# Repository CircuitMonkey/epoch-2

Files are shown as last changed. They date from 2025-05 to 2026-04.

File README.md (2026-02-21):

# epoch-2
Epoch Vibrator Controller *(Haptic Field Emitter)* 2 - Now with 100% more edge...

## Description
A follow on to [Epoch 1](https://github.com/CircuitMonkey/epoch).  Designed in 2025. Replaced by [Epoch 3](https://github.com/CircuitMonkey/epoch-3) in 2026. Redesigned with [AdaFruit Qualia ESP32](https://www.adafruit.com/product/5800) and a [Amazon 4-inch IPS (GT911 touch)](https://www.amazon.com/dp/B0D9H3HWR3).  Motors driven with [pca9685 PWM controller](https://learn.adafruit.com/adafruit-16-channel-pwm-servo-hat-for-raspberry-pi)/[Amazon PCA9685 Board](https://www.amazon.com/dp/B0D73811V8) and FET outputs in order to drive bigger motors.  Epoch 1 was limited to 120mA maximum motor drive (because of PWM controller choice) and some larger "rumble" motors need 180mA or higher.

## Features
 - [Adafruit Qualia ESP32-S3 RGB666](https://www.adafruit.com/product/5800)
 - [Amazon 4-inch IPS (GT911 touch)](https://www.amazon.com/dp/B0D9H3HWR3)
 - [pca9685 PWM controller](https://learn.adafruit.com/adafruit-16-channel-pwm-servo-hat-for-raspberry-pi)
 - [LiPo Battery - 62mm x 50mm, 2500mAH, Adafruit](https://www.adafruit.com/product/328)
 - TRS 3.5mm type cables (two motors per connector)
 - FET outputs in order to drive bigger motors.
 - Used [Electric Mini Micro Vibration Motor DC 1.5V/3V/6V 1000RPM M20 with Brass Eccentric Rotating Wheel ](https://www.amazon.com/dp/B07X7MKKQH) in attachments.
 - Programmed in CircuitPython.

## Dev Notes
 - Hardware was intended to output all 16 channels as two rows of connectors, but only built one row.
 - IPS type display used most of the ESP32 pins.
 - Circuit Python with the IPS display was excrucatingly slow.
 - Touch response time was very slow with Circuit Python and made on-screen sliders frustrating to use.
 - TRS Audio type connectors were a big improvement over Molex MinifitJr type connectors.
 - This platform performed well for almost a year, before Epoch-3 developed.
 - Experimental air pressure input showed promise but was fussy in setup/use and not worth using long term.
 - PCA9685 PWM driver was much easier to code with over older Epoch-1 PWM driver.
 - FET outputs allowed use of slightly bigger motors with more rumble yet allowed for a lower motor speeds for subtle haptic sensations.
 - Custom molds were 3D printed for attachments where silicone was poured over a TPU flex frame that held the motors.
 - Attachments had LEDs built in to indicate intensity of each motor.
 - This design and motor patterns have changed my life, able to realize two or three hour long usage sessions.
 - I look forward to improving on this design in Epoch 3.

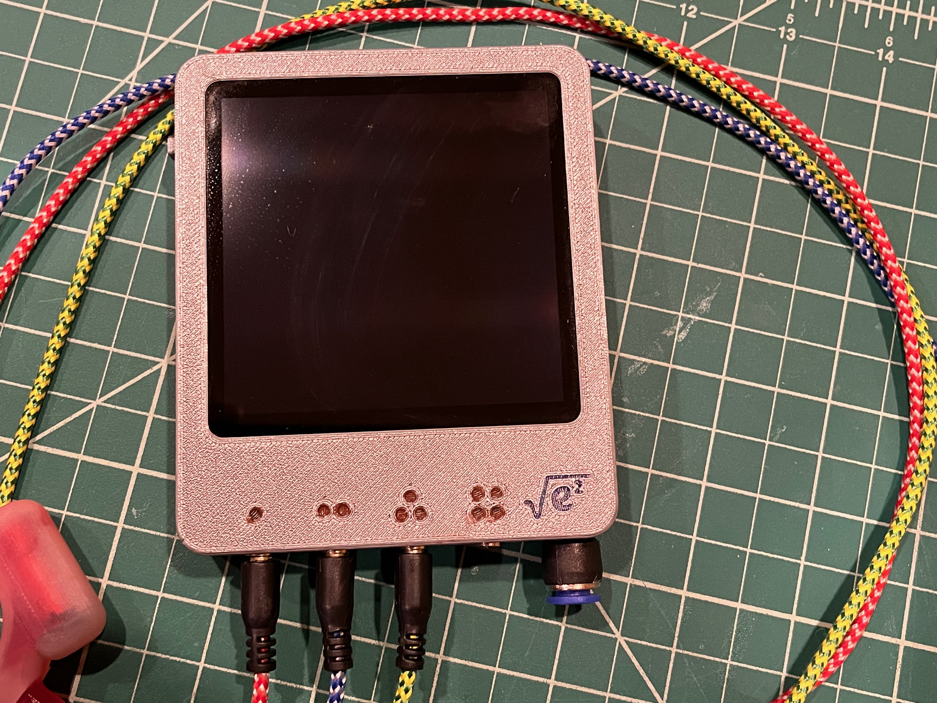
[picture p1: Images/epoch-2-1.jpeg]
Epoch 2 - Front View

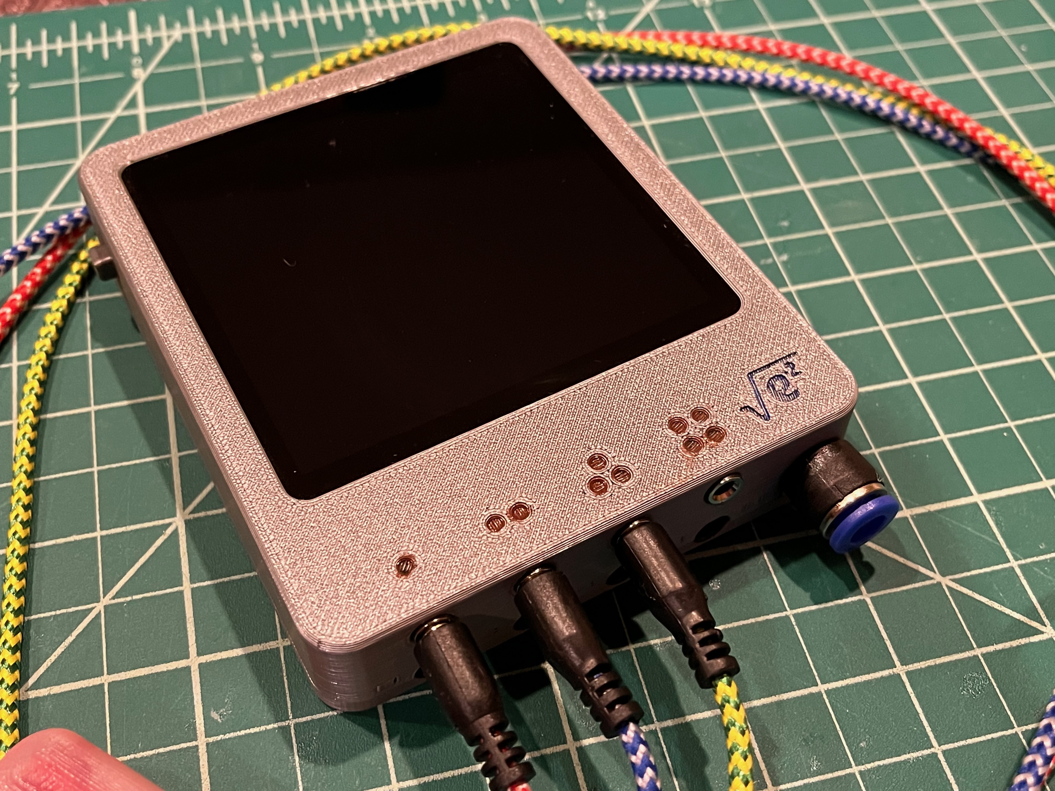
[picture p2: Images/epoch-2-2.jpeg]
Epoch 2 - Ortho View

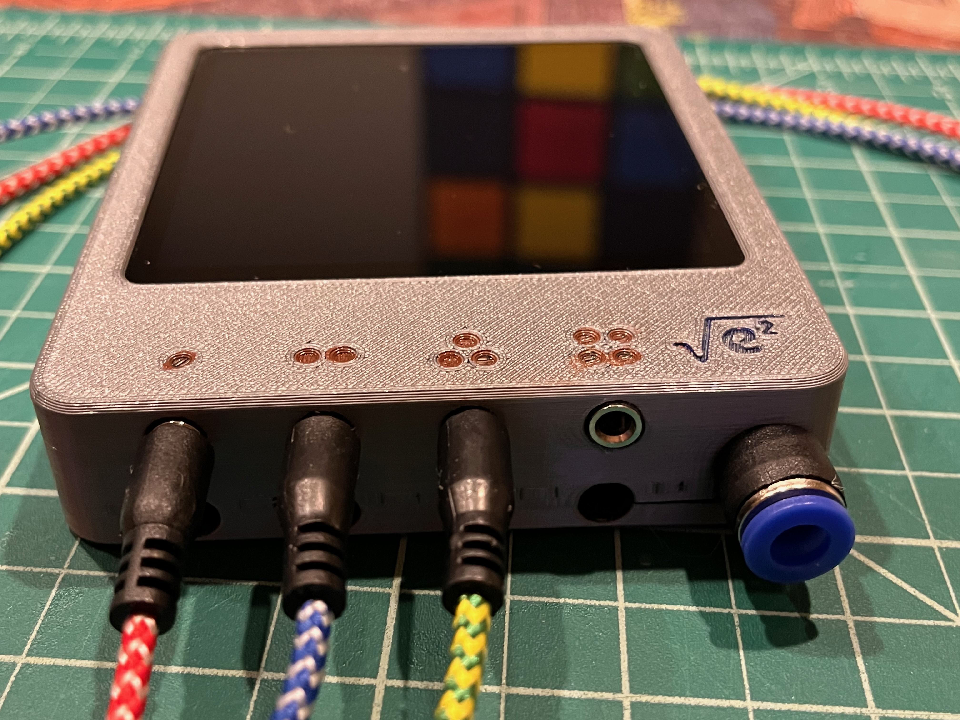
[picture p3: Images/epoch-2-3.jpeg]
Epoch 2 - Connector View

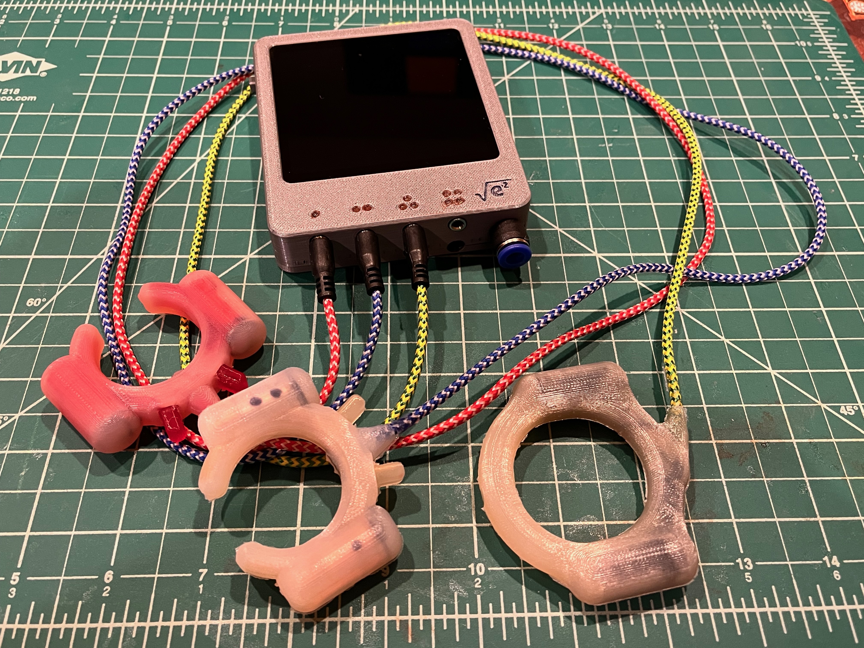
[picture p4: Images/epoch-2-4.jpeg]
Epoch 2 - With Attachments

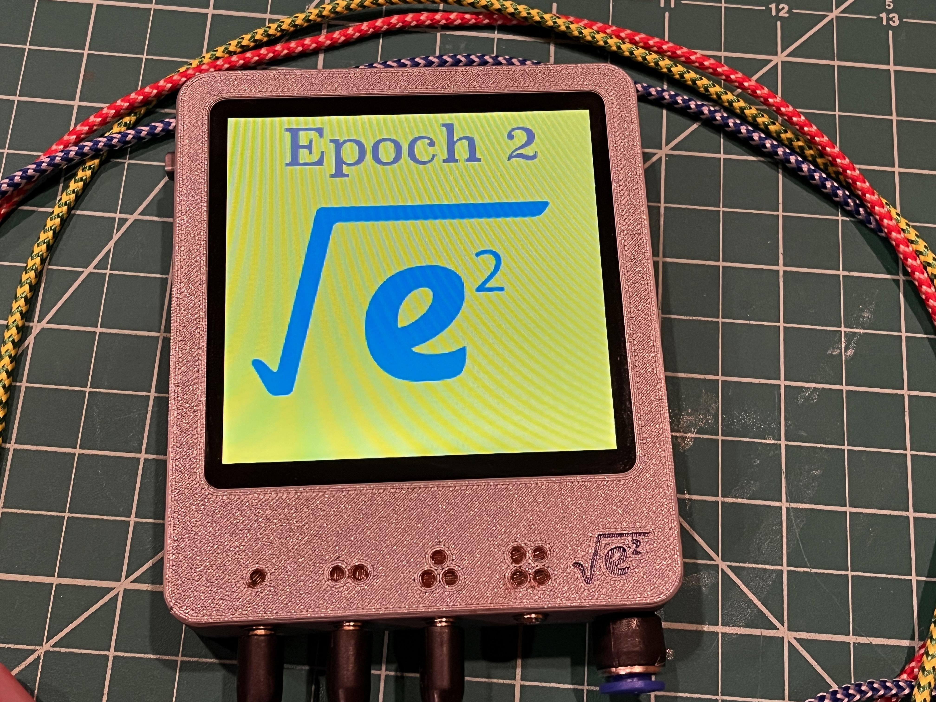
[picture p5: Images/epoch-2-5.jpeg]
Epoch 2 - Power On Screen

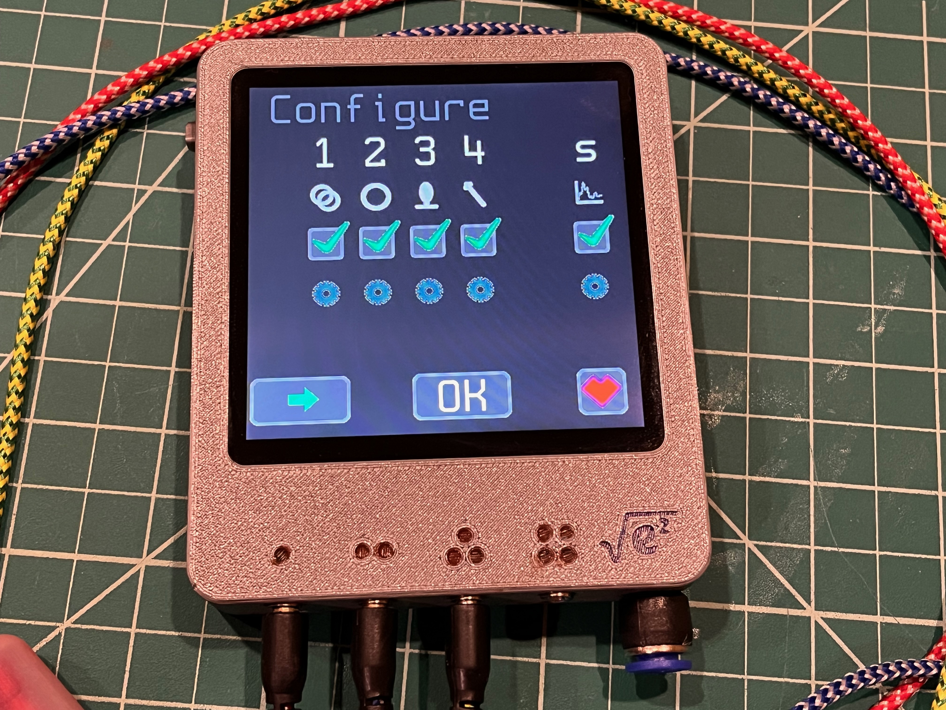
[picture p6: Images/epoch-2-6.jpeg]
Epoch 2 - Configuration Screen

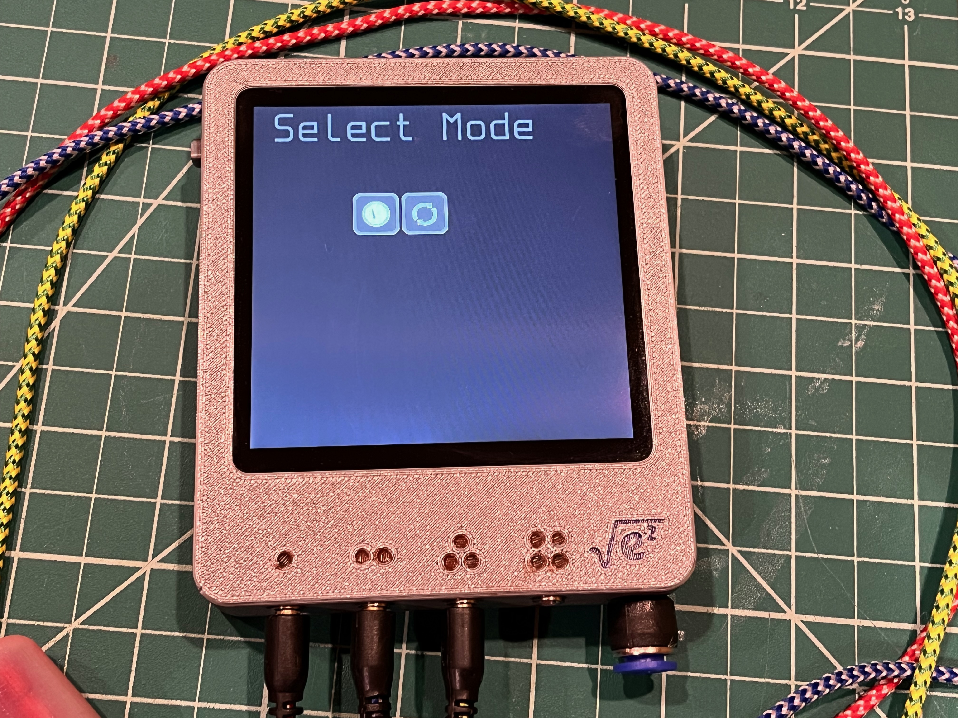
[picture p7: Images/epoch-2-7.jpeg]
Epoch 2 - Mode Select Screen

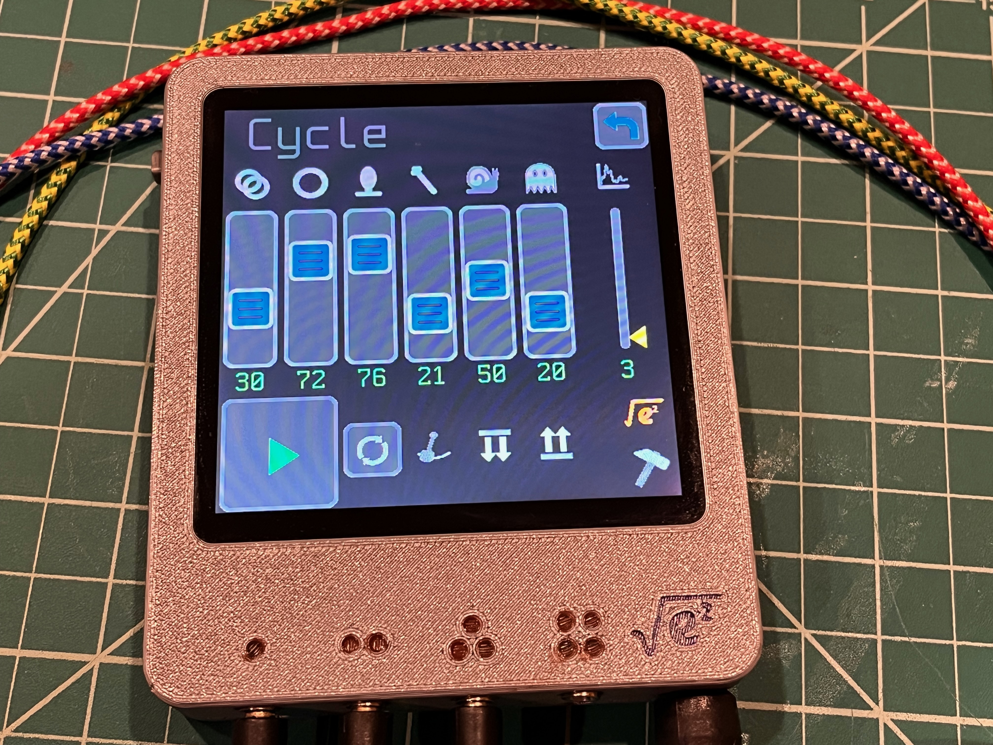
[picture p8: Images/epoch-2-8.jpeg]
Epoch 2 - Cycle Mode Screen

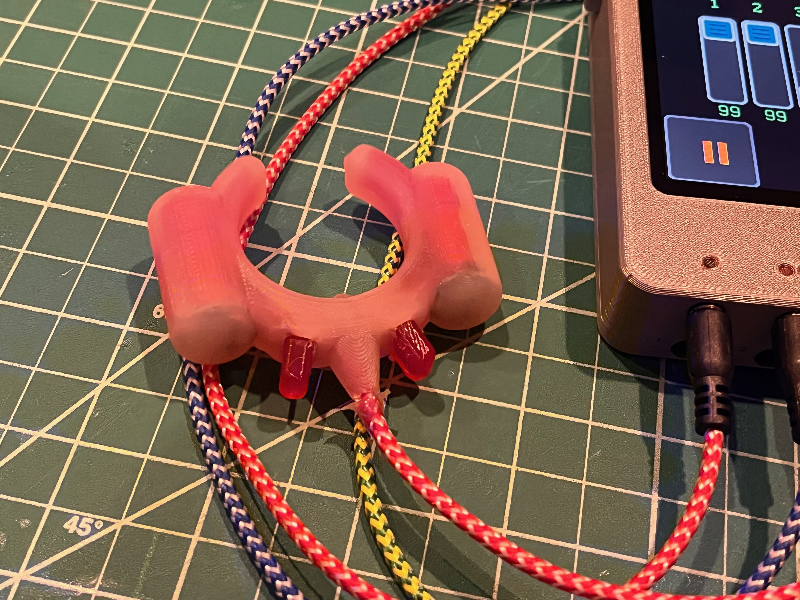
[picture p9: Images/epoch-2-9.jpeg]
Epoch 2 - Attachment Not-vibrating

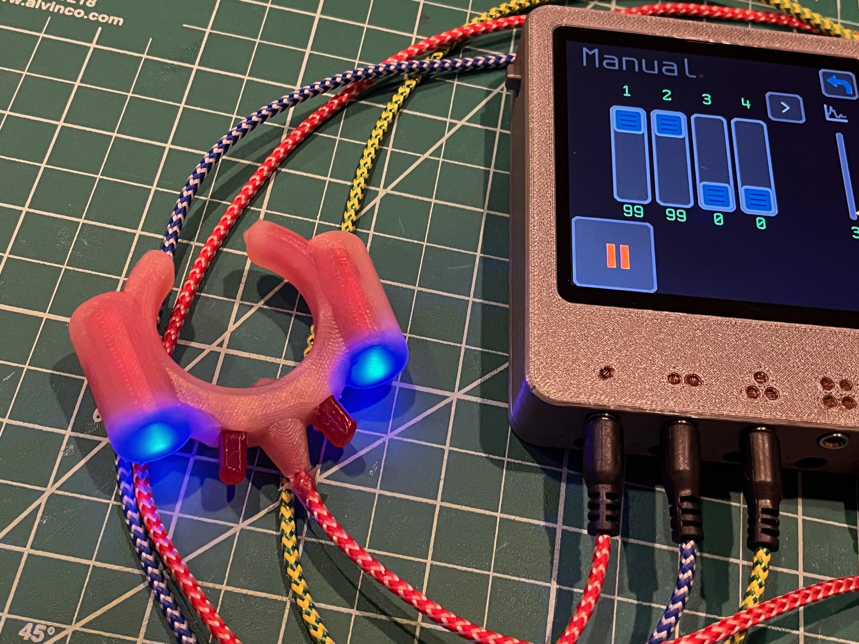
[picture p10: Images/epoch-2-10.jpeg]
Epoch 2 - Attachment Vibrating


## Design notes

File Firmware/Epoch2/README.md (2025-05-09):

# Main Program for Epoch 2

Place all files/dirs into Qualia CircuitPython drive root then reboot.

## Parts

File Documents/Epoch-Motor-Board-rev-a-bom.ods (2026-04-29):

Epoch Motor Board (Rev. A)
Reference | Qty | Value | Footprint
C1,C2,C3,C4 | 4 | 0.01uF/50V | Capacitor_SMD:C_0603_1608Metric
D1,D2,D3,D4 | 4 | BLU | LED_SMD:LED_0603_1608Metric
R1,R2,R3,R4 | 4 | 47R | Resistor_SMD:R_0603_1608Metric

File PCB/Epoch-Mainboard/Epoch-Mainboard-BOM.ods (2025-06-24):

Epoch 2 – Mainboard BOM |  | Rev. A – 2025/06
Reference | Qty | Value | Footprint | Datasheet
BAT1 | 1 | JST-PH | Connector_JST:JST_PH_S2B-PH-K_1x02_P2.00mm_Horizontal | ~
C1,C2 | 2 | 4.7uF/16V | Capacitor_SMD:C_0603_1608Metric | ~
C3 | 1 | 0.01uF | Capacitor_SMD:C_0603_1608Metric | ~
D1 | 1 | YEL | LED_SMD:LED_0603_1608Metric | ~
D2 | 1 | BLU | LED_SMD:LED_0603_1608Metric | ~
J1 | 1 | USB_C_Receptacle_PowerOnly_6P | Connector_USB:USB_C_Receptacle_HRO_TYPE-C-31-M-17 | https://www.usb.org/sites/default/files/documents/usb_type-c.zip
J2,J3 | 2 | Conn_02x06_Odd_Even | Connector_PinHeader_2.54mm:PinHeader_2x06_P2.54mm_Vertical | ~
R1,R2,R3,R4,R5,R6,R7 | 7 | 1K | Resistor_SMD:R_0603_1608Metric | ~
R8,R9 | 2 | 22K (pull up!) | Resistor_SMD:R_0603_1608Metric | ~
R10 | 1 | 2K | Resistor_SMD:R_0603_1608Metric | ~
R11,R12 | 2 | 2K | Resistor_SMD:R_0603_1608Metric | ~
R13,R14 | 2 | 0R | Resistor_SMD:R_1206_3216Metric | ~
R21,R22,R23,R24,R25,R26,R27,R28,R29,R30,R31,R32,R33,R34,R35,R36 | 16 | 220R | Resistor_SMD:R_0603_1608Metric | ~
SW1 | 1 | SW_SPDT | Button_Switch_THT:SW_Slide_SPDT_Angled_CK_OS102011MA1Q | ~
U1 | 1 | PCA9685PW | Package_SO:TSSOP-28_4.4x9.7mm_P0.65mm | http://www.nxp.com/docs/en/data-sheet/PCA9685.pdf
U2 | 1 | MCP73831T-2ACI/OT | Package_TO_SOT_SMD:SOT-23-5 | http://ww1.microchip.com/downloads/en/DeviceDoc/20001984g.pdf

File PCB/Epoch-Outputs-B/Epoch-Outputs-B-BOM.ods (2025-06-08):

Epoch 2 – Outputs B - BOM |  | Rev. A – 2025/06
Reference | Qty | Value | Footprint | Datasheet
C1,C2,C3,C4 | 4 | 22uF/16V | Capacitor_SMD:C_1812_4532Metric | ~
D1,D2,D3,D4,D5,D6,D7,D8 | 8 | NRVA4007T3G | Diode_SMD:D_SMA | http://www.onsemi.com/pub_link/Collateral/MRA4003T3-D.PDF
F1,F2,F3,F4 | 4 | MF-MSMF075 | Resistor_SMD:R_1812_4532Metric | ~
J1,J2,J3,J4 | 4 | Jack - Tayda A-4780 | Connector_Audio:Jack_3.5mm_CUI_SJ1-3515N_Horizontal | ~
J5 | 1 | Conn_02x06_Odd_Even | Connector_PinHeader_2.54mm:PinHeader_2x06_P2.54mm_Vertical | ~
Q1,Q2,Q3,Q4,Q5,Q6,Q7,Q8 | 8 | Si1308EDL | Package_TO_SOT_SMD:SOT-323_SC-70 | https://www.vishay.com/docs/63399/si1308edl.pdf
R1,R2,R3,R4,R5,R6,R7,R8 | 8 | 100R | Resistor_SMD:R_0603_1608Metric | ~
R9,R10,R11,R12,R13,R14,R15,R16 | 8 | 100K | Resistor_SMD:R_0603_1608Metric | ~

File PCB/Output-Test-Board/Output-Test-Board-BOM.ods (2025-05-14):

Epoch2 – Motor Test Board – Rev. A |  |  | 2025-05
Reference | Qty | Value | Footprint | Datasheet
C1 | 1 | 22uF / 16V | Capacitor_SMD:C_1812_4532Metric | ~
D1,D2 | 2 | GRN | LED_SMD:LED_0603_1608Metric | ~
D3,D4 | 2 | NRVA4007T3G | Diode_SMD:D_SMA | http://www.onsemi.com/pub_link/Collateral/MRA4003T3-D.PDF
F1 | 1 | MF-MSMF075 | Resistor_SMD:R_1812_4532Metric | ~
J1 | 1 | Conn_01x04_Pin | Connector_PinHeader_2.54mm:PinHeader_1x04_P2.54mm_Vertical | ~
J2 | 1 | Jack - Tayda A-4780 | Connector_Audio:Jack_3.5mm_Ledino_KB3SPRS_Horizontal | ~
Q1,Q2 | 2 | Si1308EDL | Package_TO_SOT_SMD:SOT-323_SC-70 | https://www.vishay.com/docs/63399/si1308edl.pdf
R1,R2,R3,R4 | 4 | 220R | Resistor_SMD:R_0603_1608Metric | ~
R5,R6 | 2 | 100K | Resistor_SMD:R_0603_1608Metric | ~

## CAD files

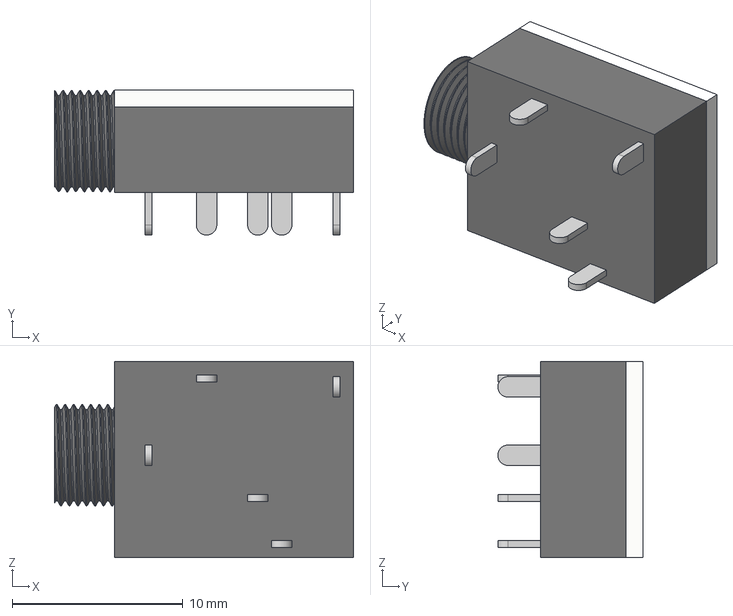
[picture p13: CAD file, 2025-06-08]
PCB/Epoch-Outputs-A/3D_models/A-069 v4.step
17.5 x 8.50 x 11.5 mm

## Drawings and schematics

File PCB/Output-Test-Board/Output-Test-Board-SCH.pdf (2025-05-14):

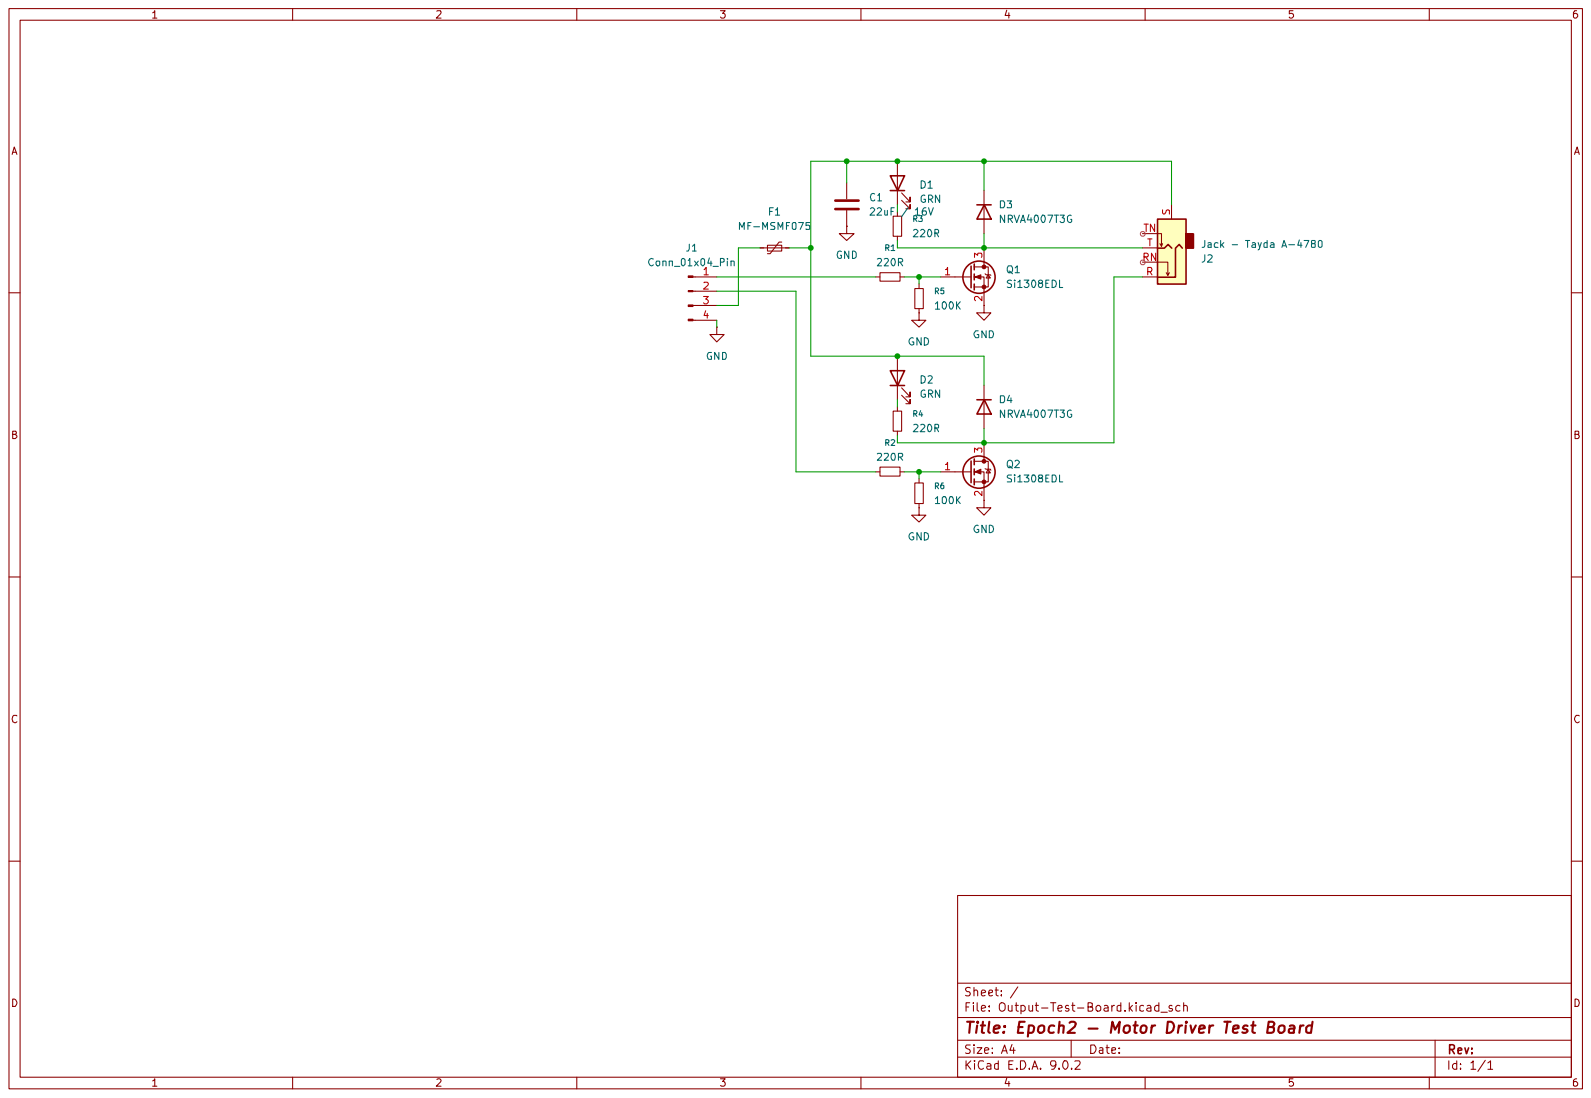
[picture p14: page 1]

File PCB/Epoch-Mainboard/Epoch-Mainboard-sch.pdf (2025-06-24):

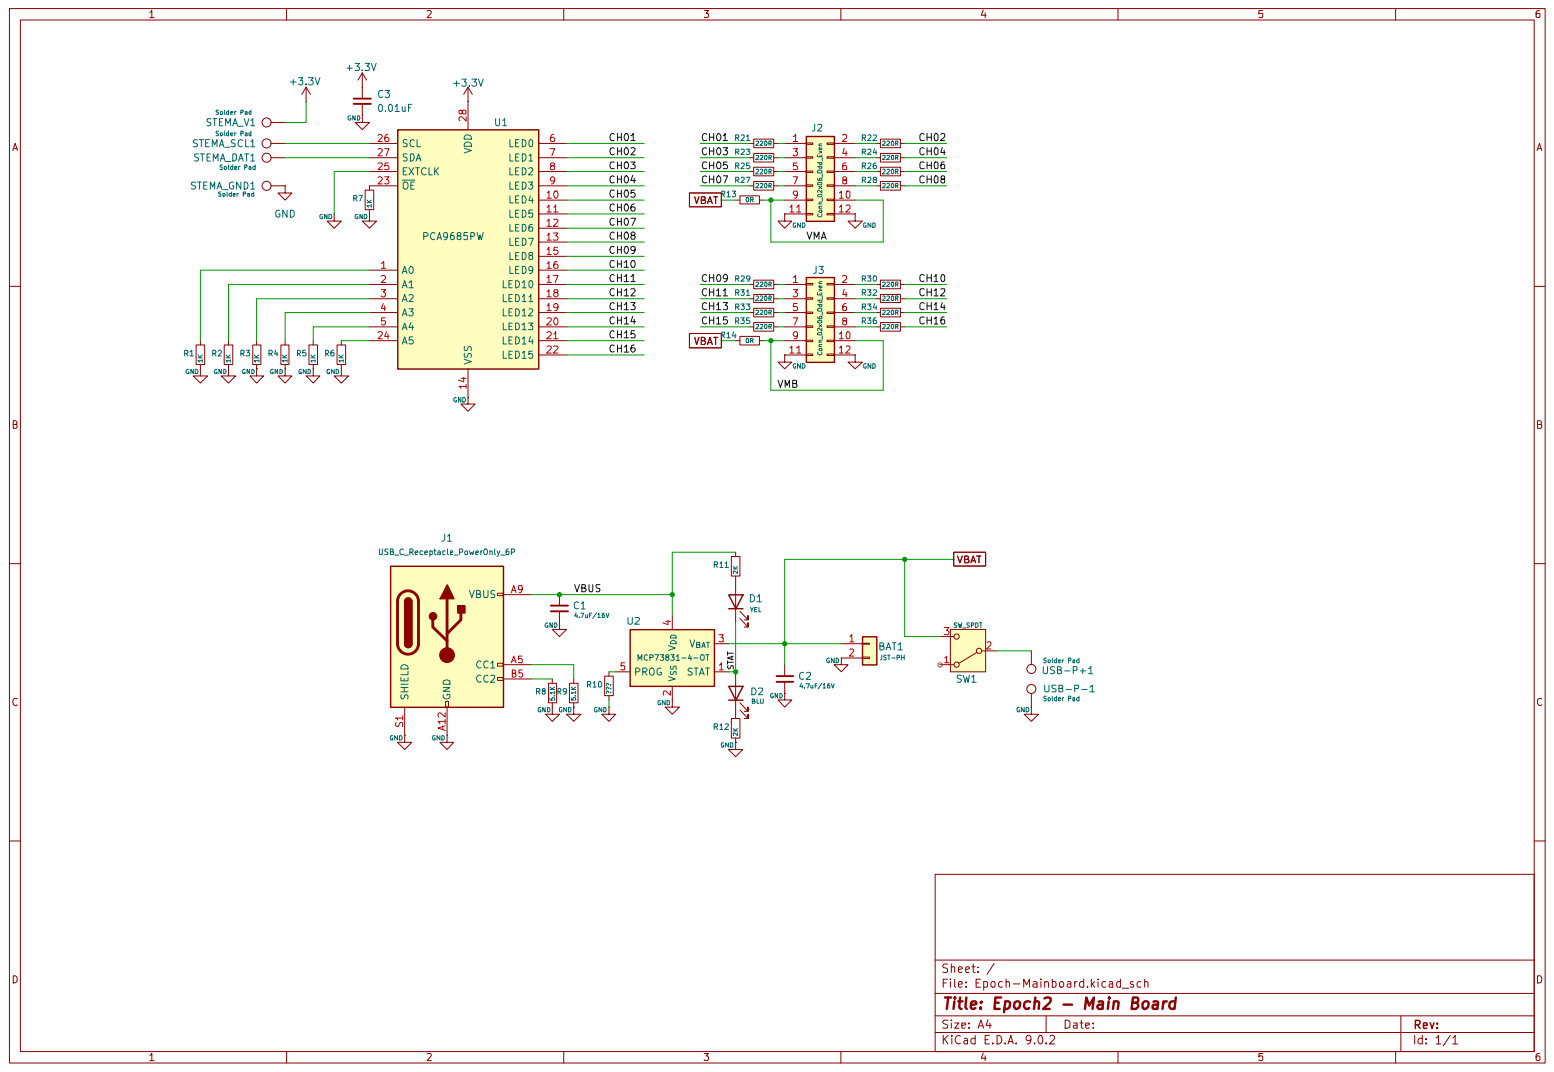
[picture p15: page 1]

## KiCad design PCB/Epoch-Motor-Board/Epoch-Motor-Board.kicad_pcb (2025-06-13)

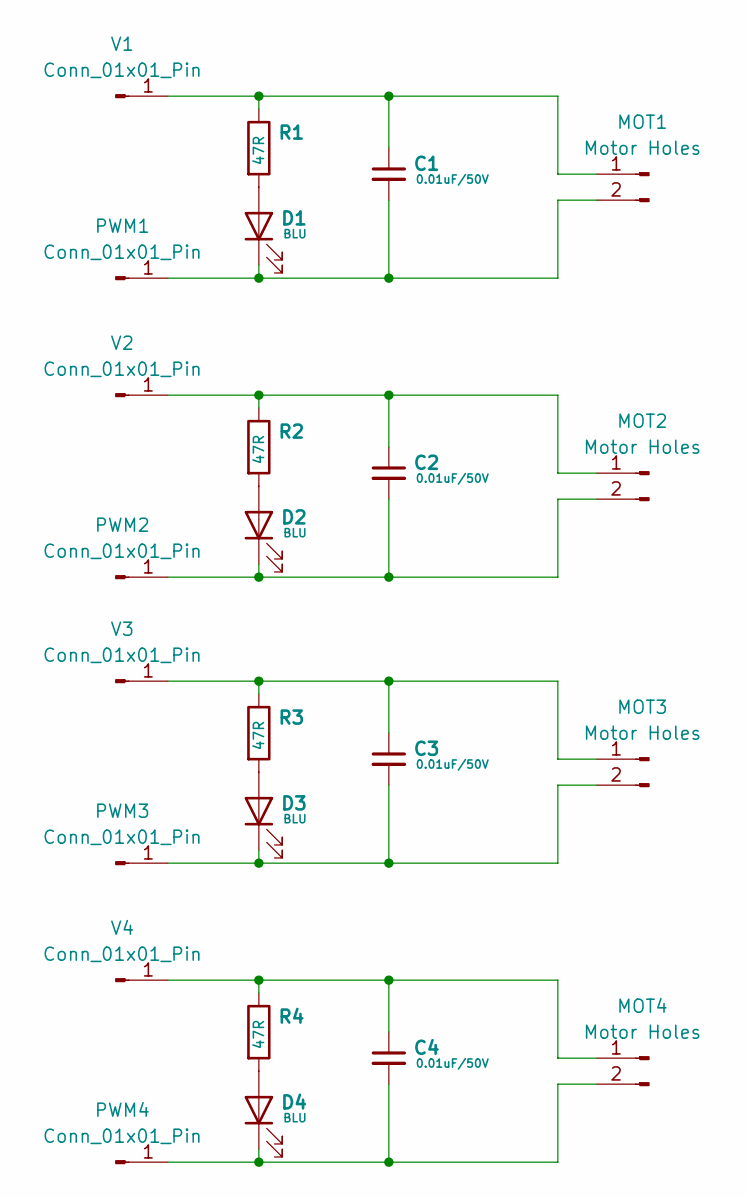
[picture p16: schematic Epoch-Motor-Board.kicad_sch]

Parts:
C1, C2, C3, C4: 0.01uF/50V; C_0603_1608Metric
D1, D2, D3, D4: BLU; LED_0603_1608Metric
MOT1, MOT2, MOT3, MOT4: Motor Holes; Motor-PCB
PWM1, PWM2, PWM3, PWM4: Conn_01x01_Pin; TestPoint_Pad_D2.0mm
R1, R2, R3, R4: 47R; R_0603_1608Metric
V1, V2, V3, V4: Conn_01x01_Pin; TestPoint_Pad_2.0x2.0mm

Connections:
unnamed: D1.2 (A), R1.2
unnamed: C1.2, D1.1 (K), MOT1.2, PWM1.1
unnamed: D2.2 (A), R2.2
unnamed: C2.2, D2.1 (K), MOT2.2, PWM2.1
unnamed: D3.2 (A), R3.2
unnamed: C3.2, D3.1 (K), MOT3.2, PWM3.1
unnamed: D4.2 (A), R4.2
unnamed: C4.2, D4.1 (K), MOT4.2, PWM4.1
unnamed: C1.1, MOT1.1, R1.1, V1.1
unnamed: C2.1, MOT2.1, R2.1, V2.1
unnamed: C3.1, MOT3.1, R3.1, V3.1
unnamed: C4.1, MOT4.1, R4.1, V4.1

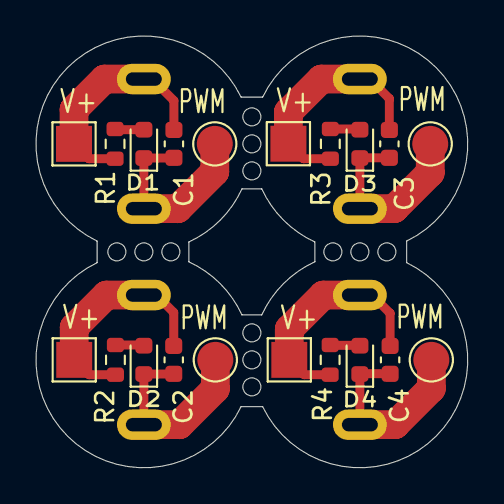
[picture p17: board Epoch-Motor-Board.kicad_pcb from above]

Board: 2 copper layers, 24.0 x 24.0 mm, 24 parts (0 on the bottom side), 12 nets.

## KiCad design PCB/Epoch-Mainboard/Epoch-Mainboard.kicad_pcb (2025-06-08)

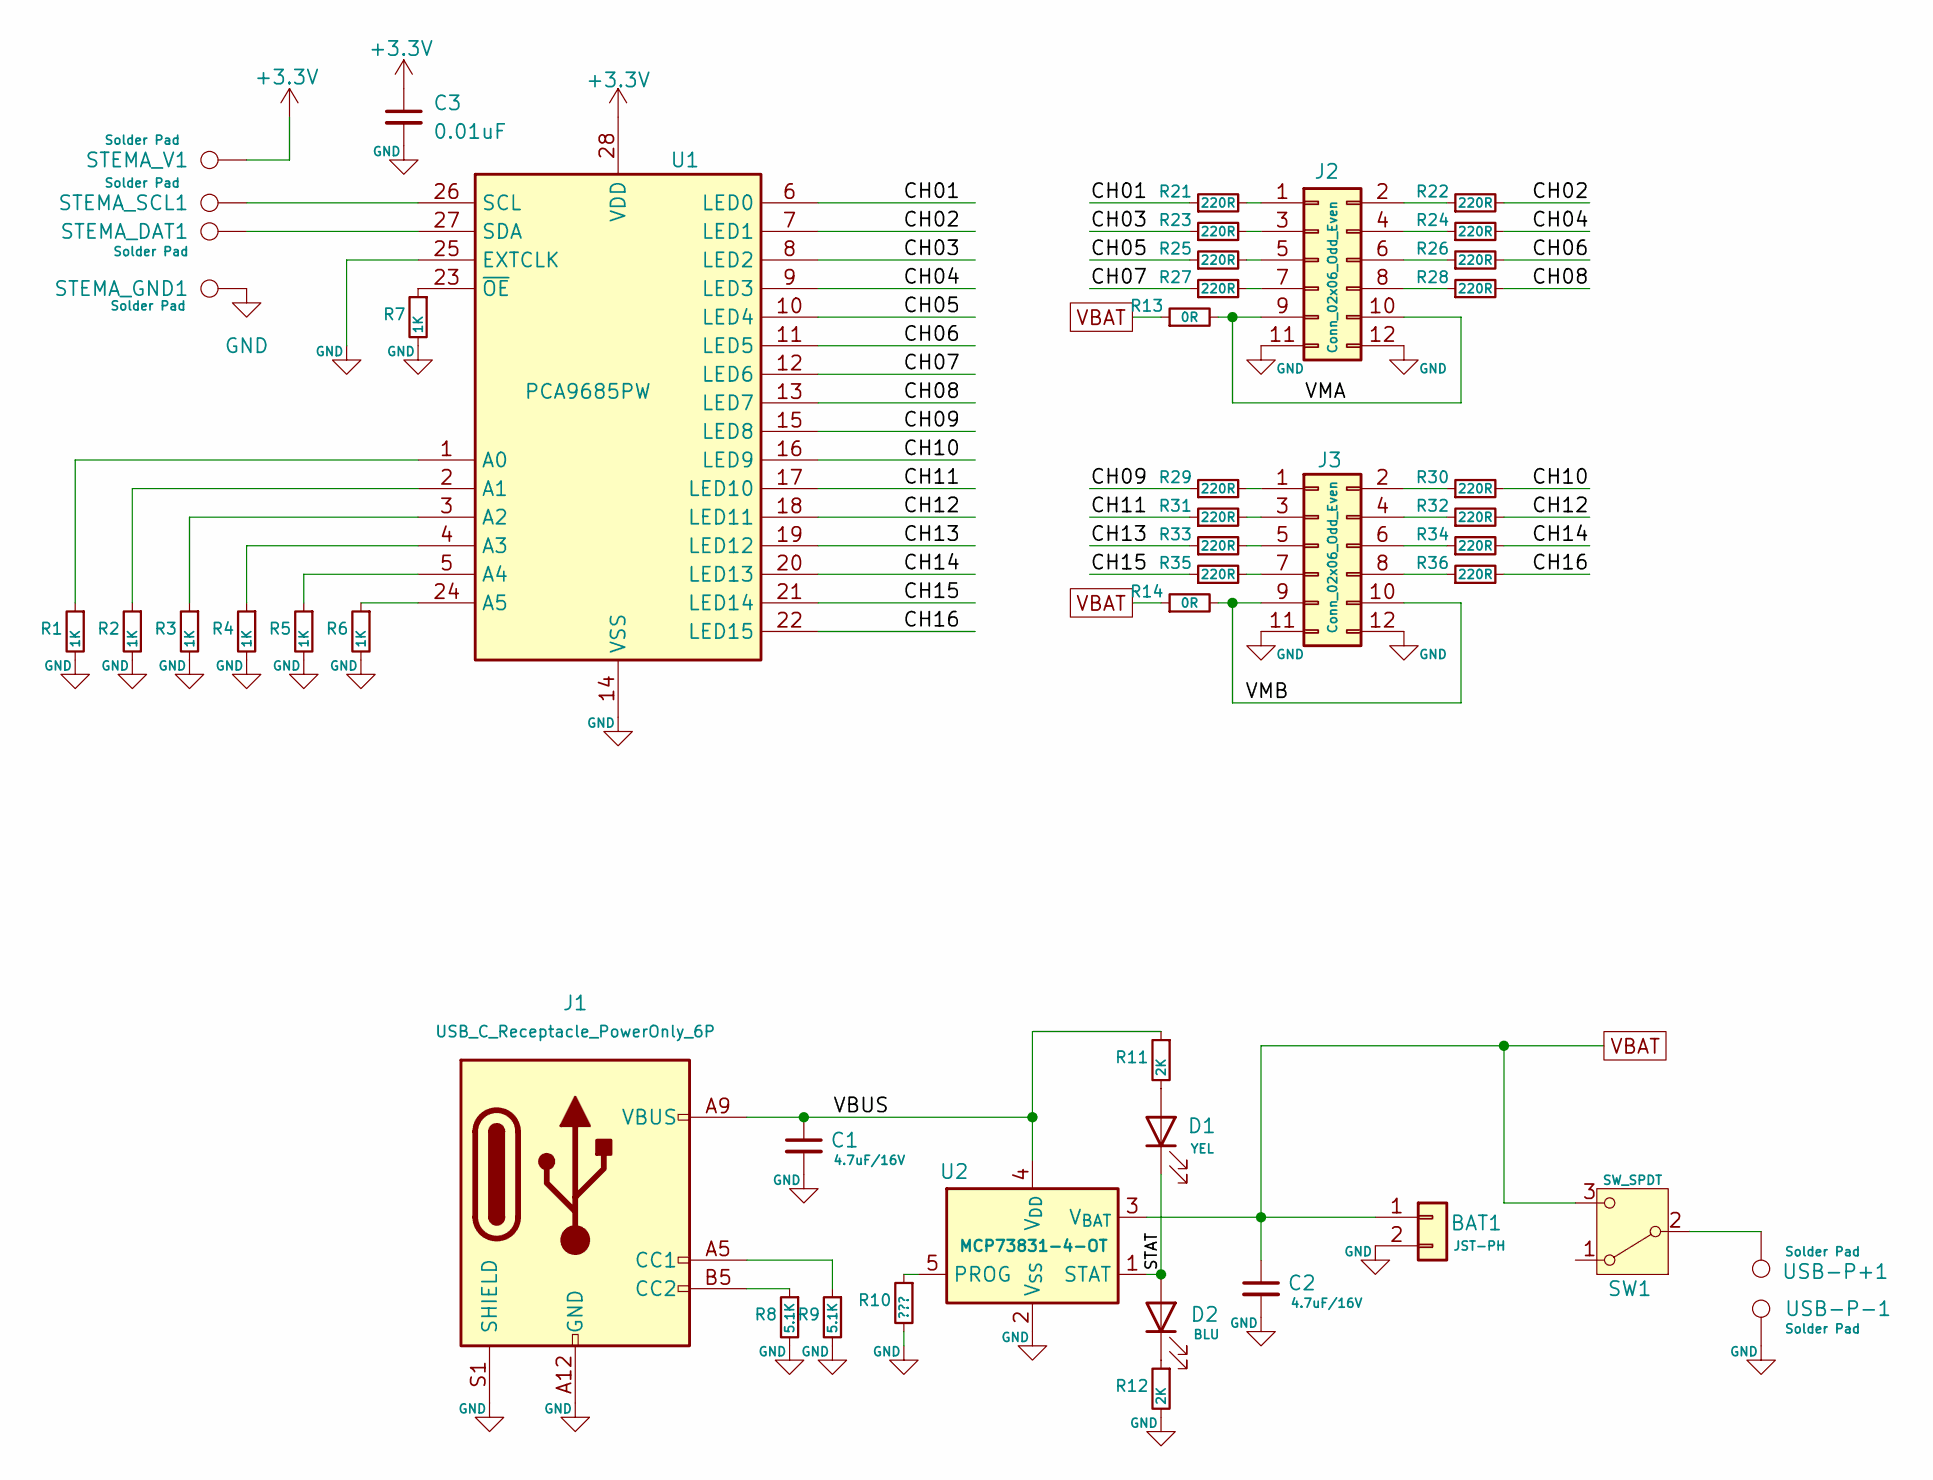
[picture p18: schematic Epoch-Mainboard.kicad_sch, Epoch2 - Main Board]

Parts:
BAT1: JST-PH; JST_PH_S2B-PH-K_1x02_P2.00mm_Horizontal
C1, C2: 4.7uF/16V; C_0603_1608Metric
C3: 0.01uF; C_0603_1608Metric
D1: YEL; LED_0603_1608Metric
D2: BLU; LED_0603_1608Metric
J1: USB_C_Receptacle_PowerOnly_6P; USB_C_Receptacle_HRO_TYPE-C-31-M-17
J2, J3: Conn_02x06_Odd_Even; PinHeader_2x06_P2.54mm_Vertical
R1, R2, R3, R4, R5, R6, R7: 1K; R_0603_1608Metric
R8, R9: 5.1K; R_0603_1608Metric
R10: ???; R_0603_1608Metric
R11, R12: 2K; R_0603_1608Metric
R13, R14: 0R; R_1206_3216Metric
R21, R22, R23, R24, R25, R26, R27, R28, R29, R30, R31, R32, R33, R34, R35, R36: 220R; R_0603_1608Metric
STEMA_DAT1: Solder Pad; TestPoint_Pad_D2.0mm
STEMA_GND1: Solder Pad; TestPoint_Pad_D2.0mm
STEMA_SCL1: Solder Pad; TestPoint_Pad_D2.0mm
STEMA_V1: Solder Pad; TestPoint_Pad_D2.0mm
SW1: SW_SPDT; SW_Slide_SPDT_Angled_CK_OS102011MA1Q
U1: PCA9685PW; TSSOP-28_4.4x9.7mm_P0.65mm
U2: MCP73831-4-OT; SOT-23-5
USB-P+1: Solder Pad; TestPoint_Pad_D2.0mm
USB-P-1: Solder Pad; TestPoint_Pad_D2.0mm

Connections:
+3.3V: C3.1, STEMA_V1.1, U1.28 (VDD)
/CH01: R21.1, U1.6 (LED0)
/CH02: R22.2, U1.7 (LED1)
/CH03: R23.1, U1.8 (LED2)
/CH04: R24.2, U1.9 (LED3)
/CH05: R25.1, U1.10 (LED4)
/CH06: R26.2, U1.11 (LED5)
/CH07: R27.1, U1.12 (LED6)
/CH08: R28.2, U1.13 (LED7)
/CH09: R29.1, U1.15 (LED8)
/CH10: R30.2, U1.16 (LED9)
/CH11: R31.1, U1.17 (LED10)
/CH12: R32.2, U1.18 (LED11)
/CH13: R33.1, U1.19 (LED12)
/CH14: R34.2, U1.20 (LED13)
/CH15: R35.1, U1.21 (LED14)
/CH16: R36.2, U1.22 (LED15)
/STAT: D1.1 (K), D2.2 (A), U2.1 (STAT)
/VBUS: C1.1, J1.A9 (VBUS), J1.B9 (VBUS), R11.1, U2.4 (V_{DD})
/VMA: J2.9, J2.10, R13.2
/VMB: J3.9, J3.10, R14.2
GND: BAT1.2, C1.2, C2.2, C3.2, J1.A12 (GND), J1.B12 (GND), J1.S1 (SHIELD), J2.11, J2.12, J3.11, J3.12, R1.2, R2.2, R3.2, R4.2, R5.2, R6.2, R7.2, R8.2, R9.2, R10.2, R12.2, STEMA_GND1.1, U1.14 (VSS), U1.25 (EXTCLK), U2.2 (V_{SS}), USB-P-1.1
unnamed: D1.2 (A), R11.2
unnamed: D2.1 (K), R12.1
unnamed: J1.A5 (CC1), R9.1
unnamed: J1.B5 (CC2), R8.1
unnamed: J2.1, R21.2
unnamed: J2.2, R22.1
unnamed: J2.3, R23.2
unnamed: J2.4, R24.1
unnamed: J2.5, R25.2
unnamed: J2.6, R26.1
unnamed: J2.7, R27.2
unnamed: J2.8, R28.1
unnamed: J3.1, R29.2
unnamed: J3.2, R30.1
unnamed: J3.3, R31.2
unnamed: J3.4, R32.1
unnamed: J3.5, R33.2
unnamed: J3.6, R34.1
unnamed: J3.7, R35.2
unnamed: J3.8, R36.1
unnamed: SW1.2 (B), USB-P+1.1
unnamed: R1.1, U1.1 (A0)
unnamed: R2.1, U1.2 (A1)
unnamed: R3.1, U1.3 (A2)
unnamed: R4.1, U1.4 (A3)
unnamed: R5.1, U1.5 (A4)
unnamed: R6.1, U1.24 (A5)
unnamed: STEMA_SCL1.1, U1.26 (SCL)
unnamed: STEMA_DAT1.1, U1.27 (SDA)
unnamed: R7.1, U1.23 (~OE)
unnamed: R10.1, U2.5 (PROG)
VBAT: BAT1.1, C2.1, R13.1, R14.1, SW1.3 (C), U2.3 (V_{BAT})

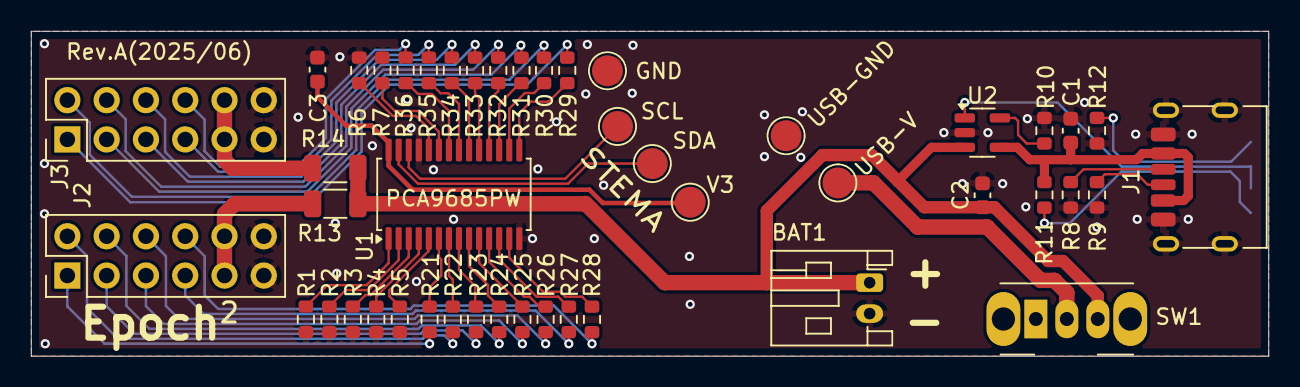
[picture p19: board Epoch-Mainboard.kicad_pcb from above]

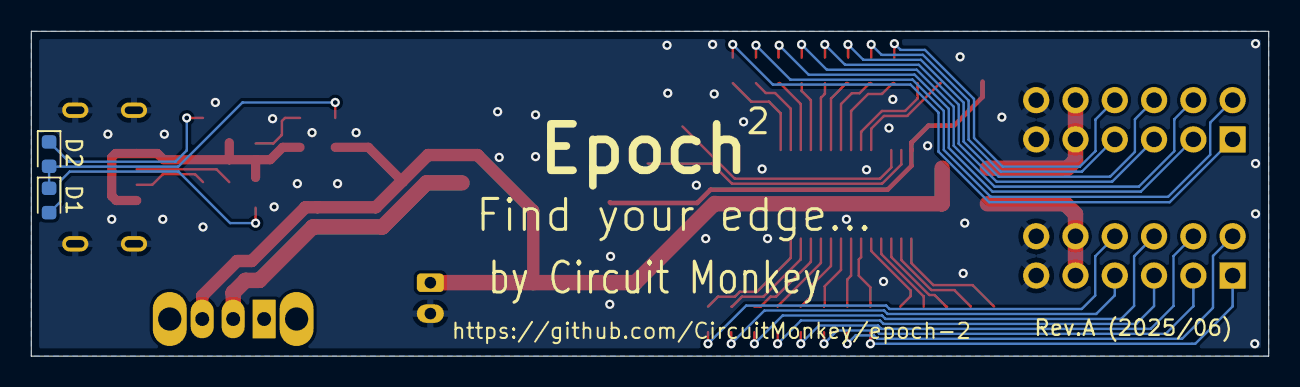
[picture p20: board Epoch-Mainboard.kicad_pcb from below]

Board: 2 copper layers, 80.0 x 21.0 mm, 48 parts (2 on the bottom side), 54 nets.

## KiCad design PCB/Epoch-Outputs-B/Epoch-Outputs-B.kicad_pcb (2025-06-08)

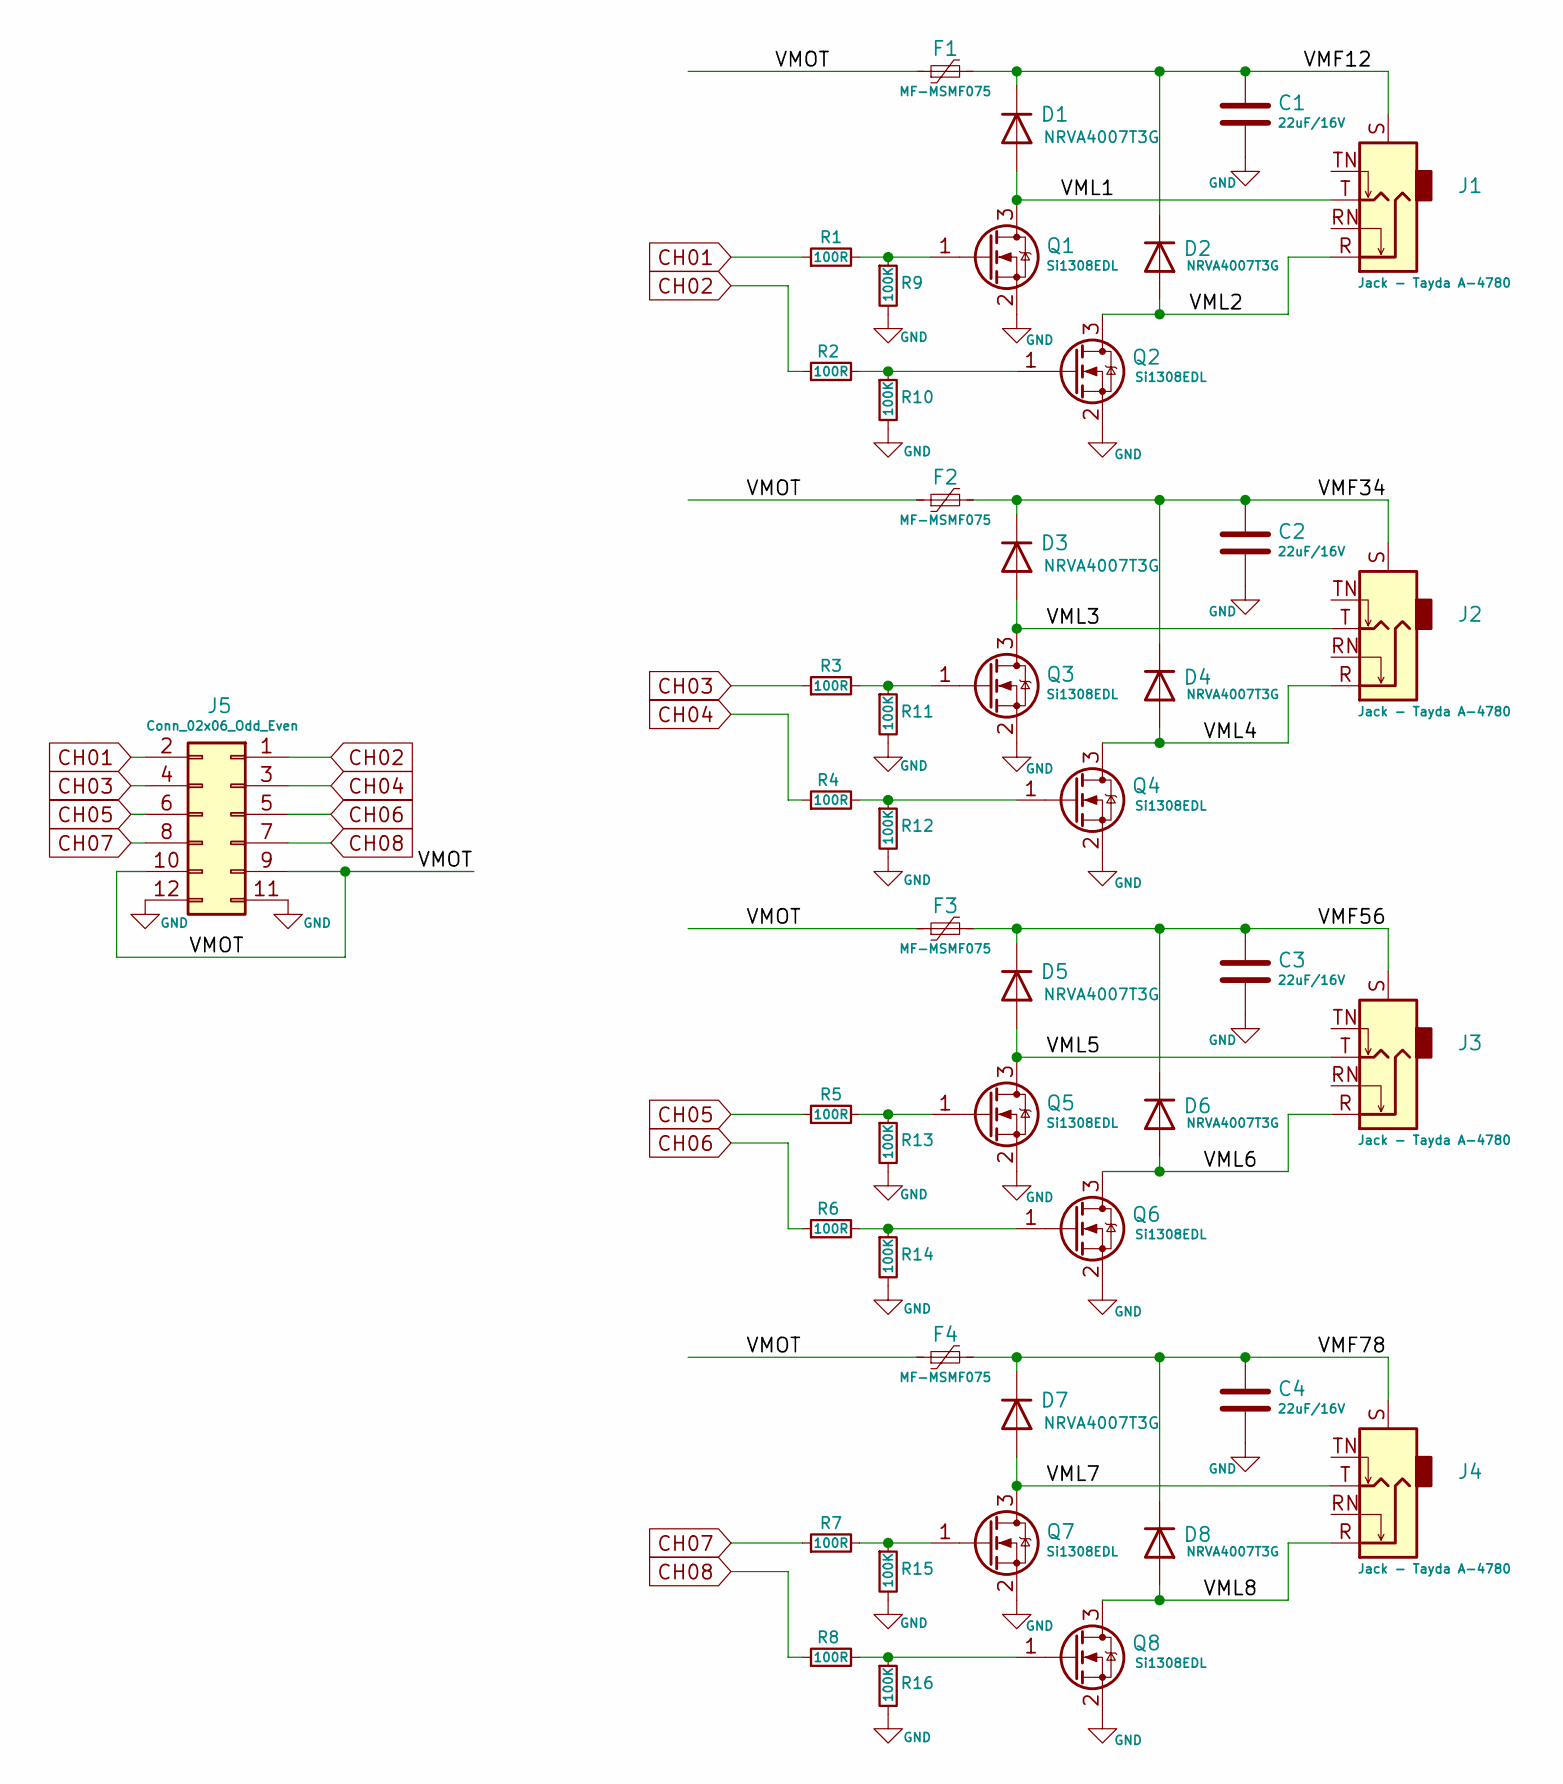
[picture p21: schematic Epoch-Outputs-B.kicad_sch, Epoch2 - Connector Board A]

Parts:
C1, C2, C3, C4: 22uF/16V; C_1812_4532Metric
D1, D2, D3, D4, D5, D6, D7, D8: NRVA4007T3G; D_SMA
F1, F2, F3, F4: MF-MSMF075; R_1812_4532Metric
J1, J2, J3, J4: Jack - Tayda A-4780; Jack_3.5mm_CUI_SJ1-3515N_Horizontal
J5: Conn_02x06_Odd_Even; PinHeader_2x06_P2.54mm_Vertical
Q1, Q2, Q3, Q4, Q5, Q6, Q7, Q8: Si1308EDL; SOT-323_SC-70
R1, R2, R3, R4, R5, R6, R7, R8: 100R; R_0603_1608Metric
R9, R10, R11, R12, R13, R14, R15, R16: 100K; R_0603_1608Metric

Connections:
/VMF12: C1.1, D1.1 (K), D2.1 (K), F1.2, J1.S
/VMF34: C2.1, D3.1 (K), D4.1 (K), F2.2, J2.S
/VMF56: C3.1, D5.1 (K), D6.1 (K), F3.2, J3.S
/VMF78: C4.1, D7.1 (K), D8.1 (K), F4.2, J4.S
/VML1: D1.2 (A), J1.T, Q1.3 (D)
/VML2: D2.2 (A), J1.R, Q2.3 (D)
/VML3: D3.2 (A), J2.T, Q3.3 (D)
/VML4: D4.2 (A), J2.R, Q4.3 (D)
/VML5: D5.2 (A), J3.T, Q5.3 (D)
/VML6: D6.2 (A), J3.R, Q6.3 (D)
/VML7: D7.2 (A), J4.T, Q7.3 (D)
/VML8: D8.2 (A), J4.R, Q8.3 (D)
/VMOT: F1.1, F2.1, F3.1, F4.1, J5.9, J5.10
CH01: J5.2, R1.1
CH02: J5.1, R2.1
CH03: J5.4, R3.1
CH04: J5.3, R4.1
CH05: J5.6, R5.1
CH06: J5.5, R6.1
CH07: J5.8, R7.1
CH08: J5.7, R8.1
GND: C1.2, C2.2, C3.2, C4.2, J5.11, J5.12, Q1.2 (S), Q2.2 (S), Q3.2 (S), Q4.2 (S), Q5.2 (S), Q6.2 (S), Q7.2 (S), Q8.2 (S), R9.2, R10.2, R11.2, R12.2, R13.2, R14.2, R15.2, R16.2
unnamed: Q1.1 (G), R1.2, R9.1
unnamed: Q2.1 (G), R2.2, R10.1
unnamed: Q3.1 (G), R3.2, R11.1
unnamed: Q4.1 (G), R4.2, R12.1
unnamed: Q5.1 (G), R5.2, R13.1
unnamed: Q6.1 (G), R6.2, R14.1
unnamed: Q7.1 (G), R7.2, R15.1
unnamed: Q8.1 (G), R8.2, R16.1

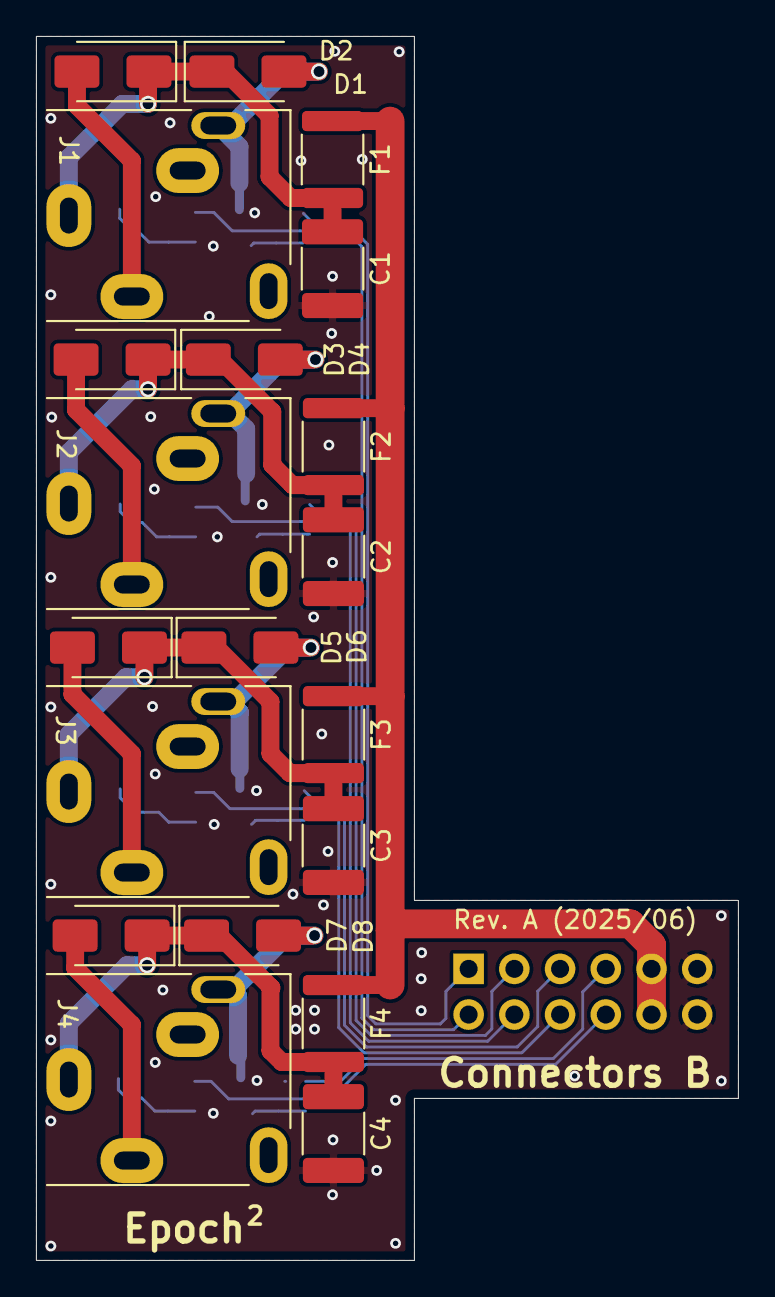
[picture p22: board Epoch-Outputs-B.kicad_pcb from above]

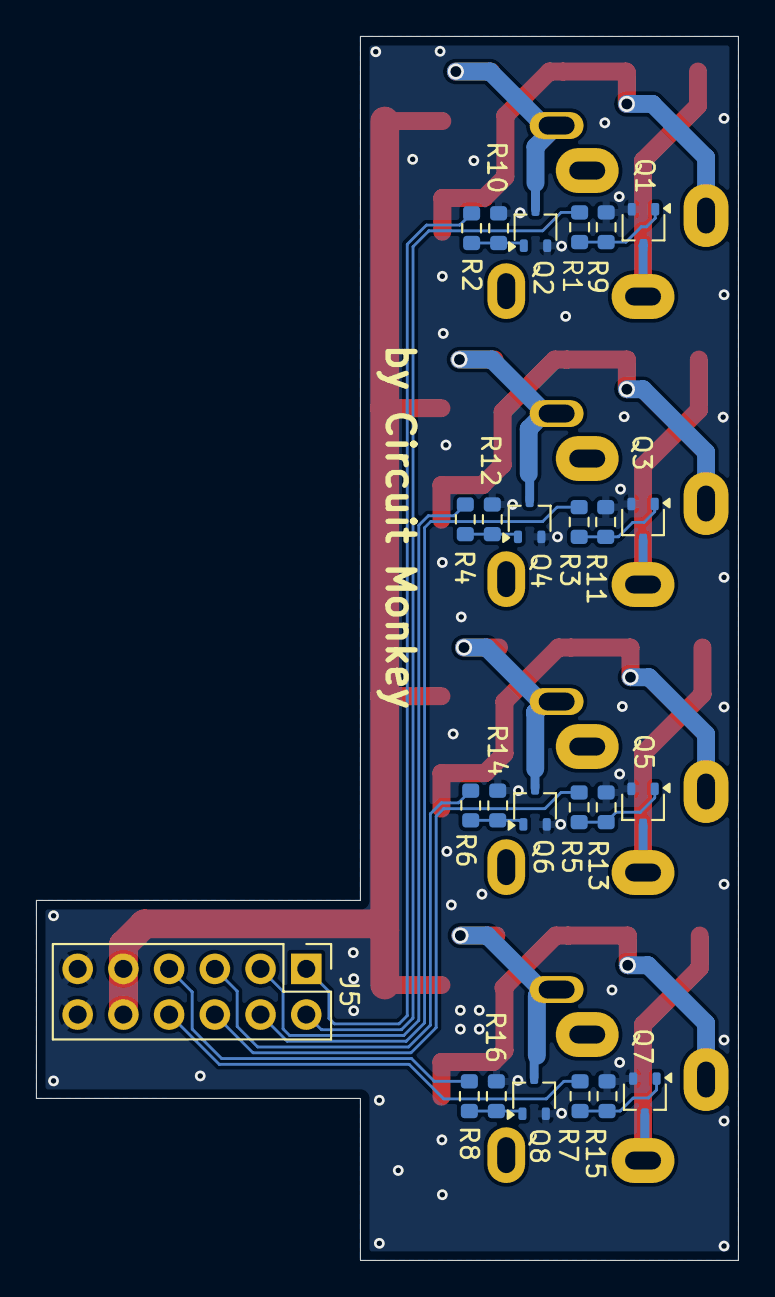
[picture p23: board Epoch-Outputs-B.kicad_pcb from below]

Board: 2 copper layers, 39.0 x 68.0 mm, 45 parts (25 on the bottom side), 30 nets.

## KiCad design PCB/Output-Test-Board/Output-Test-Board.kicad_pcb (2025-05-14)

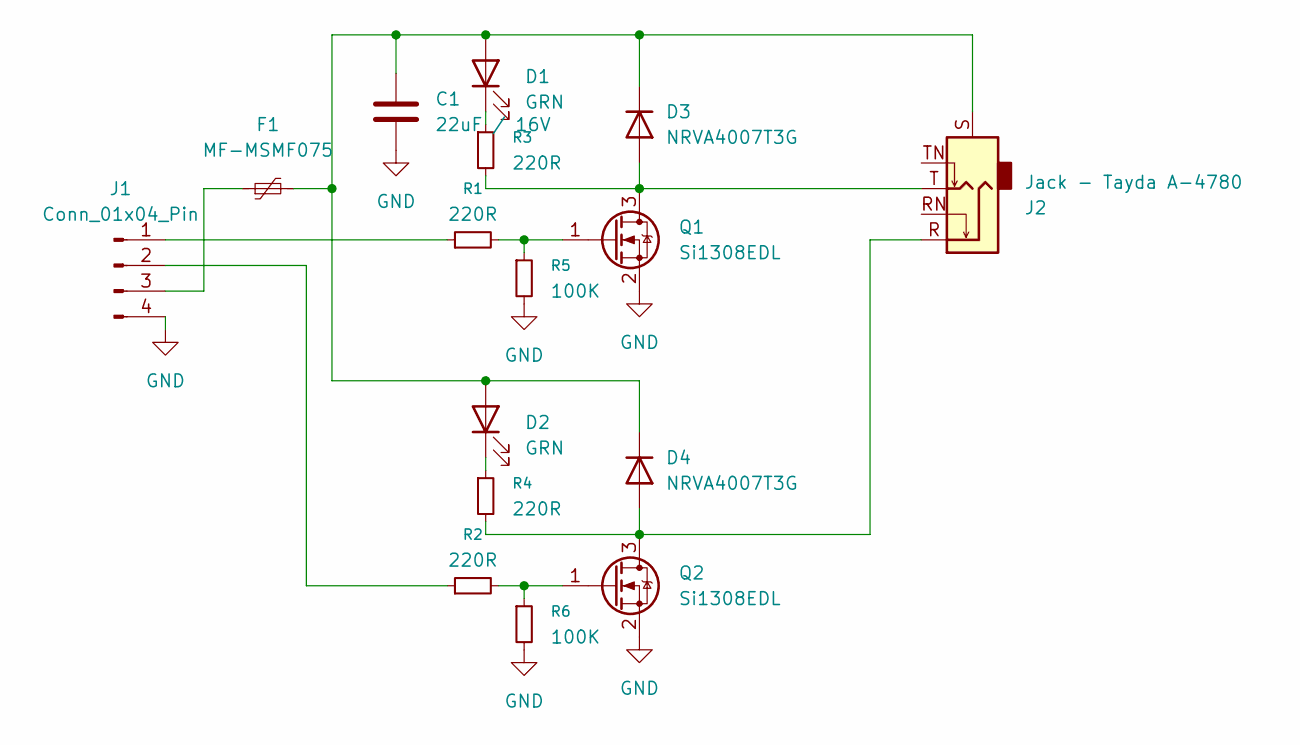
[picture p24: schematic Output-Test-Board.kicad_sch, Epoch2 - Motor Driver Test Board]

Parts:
C1: 22uF / 16V; C_1812_4532Metric
D1, D2: GRN; LED_0603_1608Metric
D3, D4: NRVA4007T3G; D_SMA
F1: MF-MSMF075; R_1812_4532Metric
J1: Conn_01x04_Pin; PinHeader_1x04_P2.54mm_Vertical
J2: Jack - Tayda A-4780; Jack_3.5mm_Ledino_KB3SPRS_Horizontal
Q1, Q2: Si1308EDL; SOT-323_SC-70
R1, R2, R3, R4: 220R; R_0603_1608Metric
R5, R6: 100K; R_0603_1608Metric

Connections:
GND: C1.2, J1.4, Q1.2 (S), Q2.2 (S), R5.2, R6.2
unnamed: C1.1, D1.2 (A), D2.2 (A), D3.1 (K), D4.1 (K), F1.2, J2.S
unnamed: D1.1 (K), R3.1
unnamed: D2.1 (K), R4.1
unnamed: D3.2 (A), J2.T, Q1.3 (D), R3.2
unnamed: D4.2 (A), J2.R, Q2.3 (D), R4.2
unnamed: J1.1, R1.1
unnamed: J1.2, R2.1
unnamed: F1.1, J1.3
unnamed: Q1.1 (G), R1.2, R5.1
unnamed: Q2.1 (G), R2.2, R6.1

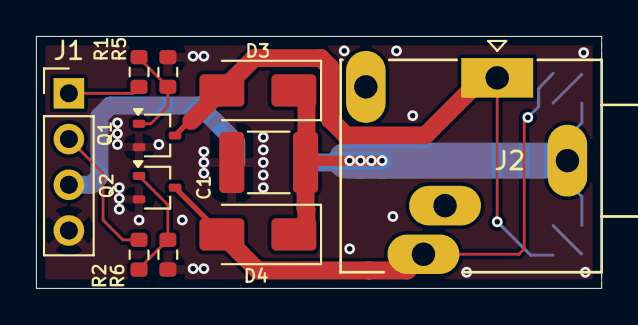
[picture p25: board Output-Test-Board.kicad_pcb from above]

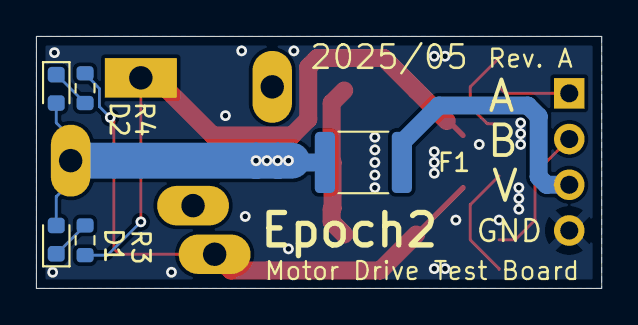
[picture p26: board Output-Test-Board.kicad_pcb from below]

Board: 2 copper layers, 31.4 x 14.0 mm, 16 parts (5 on the bottom side), 11 nets.

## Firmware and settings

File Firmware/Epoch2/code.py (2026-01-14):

# Uses some 'displayio' code from AdaFruit Qualia ESP32-S3 examples.
# SPDX-FileCopyrightText: 2021 ladyada for Adafruit Industries
# SPDX-License-Identifier: MIT
"""
    Epoch 2 Vibrator Controller using the Adafruit Qualia ESP32-S3 RGB666
    with the 4.0" square display and GT911 captouch driver

    by Mark J. Koch - c2025

    Provided under MIT license.
"""
import board
import displayio
import busio
import dotclockframebuffer
from framebufferio import FramebufferDisplay
import gt911
import adafruit_imageload
import time
from adafruit_display_shapes.rect import Rect
from adafruit_bitmap_font import bitmap_font
from adafruit_display_text.label import Label
from gui.ManualPage import *
from gui.CyclicModesPage import *
from gui.ModeSelectPage import ModeSelectPage
from gui.ConfigurePage import ConfigurePage
from gui.ChannelSettingsPage import ChannelSettingsPage
from gui.FavesPage import *
from Motors import *
import framebuffer
import state
import time
from Hx710b import *

# import supervisor
# supervisor.runtime.autoreload = False

def switchPage( st, img, img_palette, fontS, fontL ):
    print (f"Switch to Mode: {st.mode}")
    # see state.modes for list of possible modes
    if ( st.mode == 0 ): # Configure
        pg = ConfigurePage(state, img, img_palette, fontL)
    elif ( st.mode == 1 ):
        pg = ModeSelectPage(state, img, img_palette)
    elif ( st.mode == 2 ):
        pg = ManualPage(state, img, img_palette, fontS)
    elif ( st.mode == 3 ):
        pg = CyclicModesPage(state, img, img_palette, fontS)
    #elif ( st.mode == 4 ):
    #    pg = PendulumPage(state, img, img_palette, fontS)
    # elif ( st.mode == 5 ):
    #     pg = PlungeMode(state, img, img_palette, fontS)
    # elif ( st.mode == 6 ):
    #    pg = PullMode(state, img, img_palette, fontS)
    elif ( st.mode == 20 ):
        pg = ChannelSettingsPage( state, img, img_palette, fontS)
    elif ( st.mode == 30 ):
        pg = Save2FavesPage(state, img, img_palette, fontS)
    elif ( st.mode == 31 ):
        pg = LoadFromFavesPage(state, img, img_palette, fontS)
    else: # 99 Error Page?
        pg = ConfigurePage(state, img, img_palette, fontL)


    # Note: You should call display.refresh() after calling this.
    return pg


displayio.release_displays()

# Initialize the Display
tft_pins = dict(board.TFT_PINS)

board.I2C().deinit()
i2c = busio.I2C(board.SCL, board.SDA, frequency=400_000)
tft_io_expander = dict(board.TFT_IO_EXPANDER)
dotclockframebuffer.ioexpander_send_init_sequence(
    i2c, framebuffer.init_sequence_4x4_480, **tft_io_expander
)

# Sensor
sensor = Hx710b( board.A1, board.A0) # CLK, DAT

# Vibe motors
motors = Motors(i2c)
# Clear motor state right away if a reset happened.
for ch in range(16):
    motors.setMotor(ch, 0)

fb = dotclockframebuffer.DotClockFramebuffer(**tft_pins, **framebuffer.tft_timings)
display = FramebufferDisplay(fb, auto_refresh=False)
# display.auto_refresh = True

#
# Setup GUI

# State machine 0=configure (see state.py)
group = displayio.Group()
display.root_group = group
state.mode = 0

# Create a Group to hold the UI Root
bg_group = displayio.Group(scale=2)  # Scale the group by 2
group.append(bg_group)

# Splash Screen
splash_img, splash_palette = adafruit_imageload.load("gui/splash-8.png")
splash_grid = displayio.TileGrid(splash_img, pixel_shader=splash_palette)
bg_group.append(splash_grid)
display.refresh()

# Fonts
font = bitmap_font.load_font("/fonts/spleen-32x64.bdf")
sm_font = bitmap_font.load_font("/fonts/spleen-16x32.bdf")

# Screen Title
upper_label = Label(font, text="EPOCH 2", color=0x555555)
upper_label.anchor_point = (0.0, 1.0)
upper_label.anchored_position = (24, 64)
group.append(upper_label)

# Add the TileGrid to the Group
rect = Rect(0, 0, 240, 240, fill=0x222222)
bg_group.append(rect)

# call configure menu
glyphs_img, glyphs_palette = adafruit_imageload.load("gui/glyphs-8.png")

upper_label.text = state.title[state.mode]
page = ConfigurePage(state, glyphs_img, glyphs_palette, font)
group.append(page)

bg_group.remove(splash_grid)
display.refresh()

# GT911 Touch - On 4x4x480 Display
gt = gt911.GT911(i2c)


# Main Loop
drag = False
sensorCounter = 0
sensorValue = sensor.read()

while True:

    try:
        sensorCounter -= 1
        if sensorCounter < 0:
            sensorValue = sensor.read()
            sensorCounter = 5

        touches = gt.touches
        if len(touches) < 1:
            #print("No touches")
            drag = False
            page.clearTouch()
        else:
            for touch in touches:
                #x = touch[0]
                #y = touch[1]

                #TODO:  Add try-catch and turn off motors if exception
                tStat = page.handleTouch( touch, drag)
                if ( tStat == 0 ):
                    print("Touch handled.")
                    pass
                elif( tStat == 1): # touch is drag
                    print("Touch is drag")
                    #page.updateMotors(motors)
                    pass
                else: # touch is exit. tStat is code.
                    print(f"Mode returned exit page state. tstat={tStat}")
                    page.updateMotors(motors)

                    # tStat-2 is state.modes[x][ ?, ?, ?, ...] index
                    # which is the actual number for the mode to switch to
                    state.mode = state.modes[state.mode][tStat-2]
                    group.remove(page)
                    display.refresh()
                    upper_label.text = state.title[state.mode]
                    page = switchPage( state, glyphs_img, glyphs_palette, sm_font, font )
                    group.append(page)

                display.refresh()
                drag = True
                time.sleep(0.05)


        #if not drag:
        page.updateGUI( sensorValue )

        #start_time = time.monotonic()
        display.refresh()
        #end_time = time.monotonic()
        #elapsed_time = end_time - start_time
        #print("Elapsed time: ", elapsed_time, "seconds")

        page.updateMotors(motors)

    except RuntimeError:
        print("pass")
        pass

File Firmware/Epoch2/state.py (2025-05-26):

# State Machine

"""

0 = Start/Configure
1 = Mode Select
2 = Manual
3 = Cycle
4 = Pendulum
5 = Plunge
6 = Pull
...
20 = Config 1
21 = Config 2
22 = Config 3
23 = Config 4
24 = Config 5
25 = Config 6
26 = Config 7
27 = Config 8
...
30 = Save to Faves
31 = Load from Faves
"""
ch_en = [True,True,True,True,True,True,True,True,True] # 0 = Sensor

mode_manual_slider = [0,0,0,0, 0,0,0,0, 0,0,0,0, 0,0,0,0] # ch1-16

mode_cycle_slider = [50,50,50,50, 50,20] # groups 1..4 + spd + dwell
mode_cycle_motors = [0,0,0,0, 0,0,0,0, 0,0,0,0, 0,0,0,0] # ch1-16

mode_pendulum_slider = [50,50,50,50, 50,20] # groups 1..4 + spd + dwell
mode_pendulum_motors = [0,0,0,0, 0,0,0,0, 0,0,0,0, 0,0,0,0] # ch1-16

mode_plunge_slider = [50,50,50,50, 50,20] # groups 1..4 + spd + dwell
mode_plunge_motors = [0,0,0,0, 0,0,0,0, 0,0,0,0, 0,0,0,0] # ch1-16

mode_pull_slider = [50,50,50,50, 50,20] # groups 1..4 + spd + dwell
mode_pull_motors = [0,0,0,0, 0,0,0,0, 0,0,0,0, 0,0,0,0] # ch1-16

paused = True

modes = [
    [1, 30, 31, 20, 21, 22, 23, 24, 25, 26, 27], # 0 - Configure
    [2,3,4,5,6], # 1 - Mode Select
    [1], # 2 - Manual
    [1], # 3 - Cycle
    [1], # 4 - Pendulum
    [1], # 5 - Plunge
    [1], # 6 - Pull
    [1], # 7 - XX (future mode)
    [1], # 8 - XX
    [1], # 9 - XX
    [1], # 10 - XX
    [1], # 11 - XX
    [1], # 12 - XX
    [1], # 13 - XX
    [1], # 14 - XX
    [1], # 15 - XX
    [1], # 16 - XX
    [1], # 17 - XX
    [1], # 18 - XX
    [1], # 19 - XX
    [0], # 20 - Settings Ch. 1
    [0], # 21 - Settings Ch. 2
    [0], # 22 - Settings Ch. 3
    [0], # 23 - Settings Ch. 4
    [0], # 24 - Settings Ch. 5
    [0], # 25 - Settings Ch. 6
    [0], # 26 - Settings Ch. 7
    [0], # 27 - Settings Ch. 8
    [0], # 28 - XX (unused)
    [0], # 29 - XX (unused)
    [0], # 30 - Save to Favs
    [0]  # 31 - Load from Favs
]

mode = 0

title = ["Configure", "Select Mode",
    "Manual", "Cycle", "Pendulum", "Plunge", "Pull",
    "Unused", "Unused", "Unused", "Unused", "Unused",
    "Unused", "Unused", "Unused", "Unused", "Unused",
    "Unused", "Unused", "Unused",
    "Settings Ch. 1", "Settings Ch. 2", "Settings Ch. 3", "Settings Ch. 4",
    "Settings Ch. 5", "Settings Ch. 6", "Settings Ch. 7", "Settings Ch. 8",
    "Unused", "Unused",
    "Save Fave", "Choose Fave"
]

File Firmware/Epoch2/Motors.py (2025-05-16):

# Motor control
from adafruit_pca9685 import PCA9685

class Motors():
    def __init__(self, i2c):
        super().__init__()
        self.pca = PCA9685(i2c)
        # pca.frequency = 24  # 24 is lowest. What do motors need for rumble?
        self.pca.frequency = 24

        # Set the PWM duty cycle for channel zero to 50%.
        # duty_cycle is 16 bits to match other PWM objects
        # but the PCA9685 will only actually give 12 bits of resolution.
        # self.pca.channels[0].duty_cycle = 0x7FFF

    # while the PCA9685 takes values up to 12-bits, our range is 0-99
    # so we scale the value such that 99 is close to 12-bit max of 0xFFFF
    def setMotor( self, channel, value ):
        self.pca.channels[channel].duty_cycle = int(value * 0x1AC)   #0x7FFF ~= 50%

    def destroy(self):
        return

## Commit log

2025-04-28 Add data sheet for PWM chip.
2025-05-10 Favorites save/load buttons to those pages work now.
2025-05-14 Motor Test Board - Rev.A
    [Output-Test-Board.kicad_pcb, Output-Test-Board.kicad_sch]
2025-05-14 Add GUI and Motors update methods.
2025-05-14 Tune UI. Add update motors and ui methods.
2025-05-14 Now supports and updates motors and ui.
2025-05-16 Fix issue with motor PWM duty cycle value.
    [Motors.py]
2025-05-16 Rework page. Add group selectors.
    [ManualPage.py]
2025-05-17 Fix issue with some motors not changing.
    [ManualPage.py]
2025-05-17 Turn off motors at start of program. Update copyright.
2025-05-19 Track cycle motors value.
2025-05-19 Add motor indicators to Slider.
2025-05-19 Add Motor indicator diamond glyph.
2025-05-21 Add epoch button. improve dwell. Use isTouched for button.
2025-05-22 Epoch button fixes.
2025-05-22 Fix slider x position error.
    [CyclePage.py]
2025-05-22 Change I2C speed to 400K
2025-05-22 Use isTouched method for buttons.
2025-05-22 Use isTouched for Buttons.
2025-05-24 Button updates.
2025-05-24 Buttons take W and H now.
2025-05-26 Track other mode sliders.
2025-05-26 Move mode select buttons.
2025-05-26 Improvements to haptic envelope. Hammer, bug fix.
    [CyclicModesPage.py]
2025-05-27 Pressure sensor support.
2025-05-27 Sensor support.
2025-05-27 Tune sensor behavior.
2025-06-08 Final PCBs and update gitignore for backups.
    [Epoch-Mainboard.kicad_pcb, Epoch-Mainboard.kicad_sch, Epoch-Outputs-A.kicad_pcb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]
2025-06-08 Add STEP models for jack.
    [A-069 v4.step]
2025-06-08 Add BOMs
    [Epoch-Mainboard-BOM.ods, Epoch-Outputs-A.ods, Epoch-Outputs-B-BOM.ods]
2025-06-08 Exporting BOM added mysterious "fluff"
    [Epoch-Mainboard.kicad_sch]
2025-06-13 Add Epoch Motor Board.
    [Epoch-Motor-Board.kicad_pcb, Epoch-Motor-Board.kicad_sch]
2025-06-24 Part value changes.
    [Epoch-Mainboard-BOM.ods, Epoch-Mainboard.kicad_sch]
2025-06-30 Fix crash when API changed for ImageButton TextButton.
    [ManualPage.py]
2025-06-30 Tune soft env. Fix Cyc tick issue. First Use!!!!
    [CyclicModesPage.py]
2025-09-22 Tune how mode works. Fix motor numbering issue. Add notes.
    [CyclicModesPage.py]
2025-10-19 Tune cycle motor values.
2026-01-14 STP files for PCBa
2026-02-21 Add images. Update README. Random KiCAD housecleaning.
